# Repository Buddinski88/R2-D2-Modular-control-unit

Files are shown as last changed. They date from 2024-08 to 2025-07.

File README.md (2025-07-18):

# R2D2 Modular control unit (MCU)

## General motivation
- There are many good solutions for organizing all the control electronics for the whole selection of R2D2 bodys.
- However, none of these solutions fully met my requirements, so I designed my own interpretation of a modular control unit `the brain`.
  - Special thanks to everyone who inspired me, particularly John van Ohrs with his [R2D2 modular electronics panel by jfmvoers - Thingiverse](https://www.thingiverse.com/thing:6580609) and Tim Eebel with his [MarkIII Hinged Electronics Panel](https://www.printables.com/model/614178-markiii-hinged-electronics-panel).

## Requirements
- The module must be completely removable as a single unit to allow work on it at the workbench.
  - Everything must be possible without any special tools, i.e., plug-and-play instead of screws (almost achieved)!
- To allow access when installed, the entire unit must be hinged (no tools required for this step).
- The design must be modular, allowing it to be adapted to specific requirements.
- The design must be based on a grid (60x60mm) and offers panels ranging from `1x1` to `NxN`.

## Used Mods & Kudos

<blockquote class="callout note">
💡 <strong>NOTE:</strong> The following list contains an overview of the mods that I currently use in my Droid. It is not mandatory to use them as well, but I can confirm that they are compatible with each other.
</blockquote>

- [Battery Tray for Baddeley MKIII Astromech](https://www.printables.com/de/model/192002-battery-tray-for-baddeley-mkiii-astromech) by [Jason Charlton | Printables.com](https://www.printables.com/de/@JasonCharlton_264357) (he also has many other great mods!)
- Dome Motor Mount by [Gonz Pousada J Luis](https://www.facebook.com/groups/MrBaddeley/posts/3683034678691760/).
- Both Luis and Jason have other fantastic mods, and you should also check out [Jason's YouTube Channel](https://www.youtube.com/@jasonsR2D2).
- A special thanks to Ben from [Printed Droid](https://printed-droid.com), who provided me with the electronic components, and to Norbert A. Richartz, who is developing the AstroCan System and [BetterDuinoFirmwareV4](https://github.com/RealNobser/BetterDuinoFirmwareV4). He answered nearly all my questions and integrated some cool features.

## Images
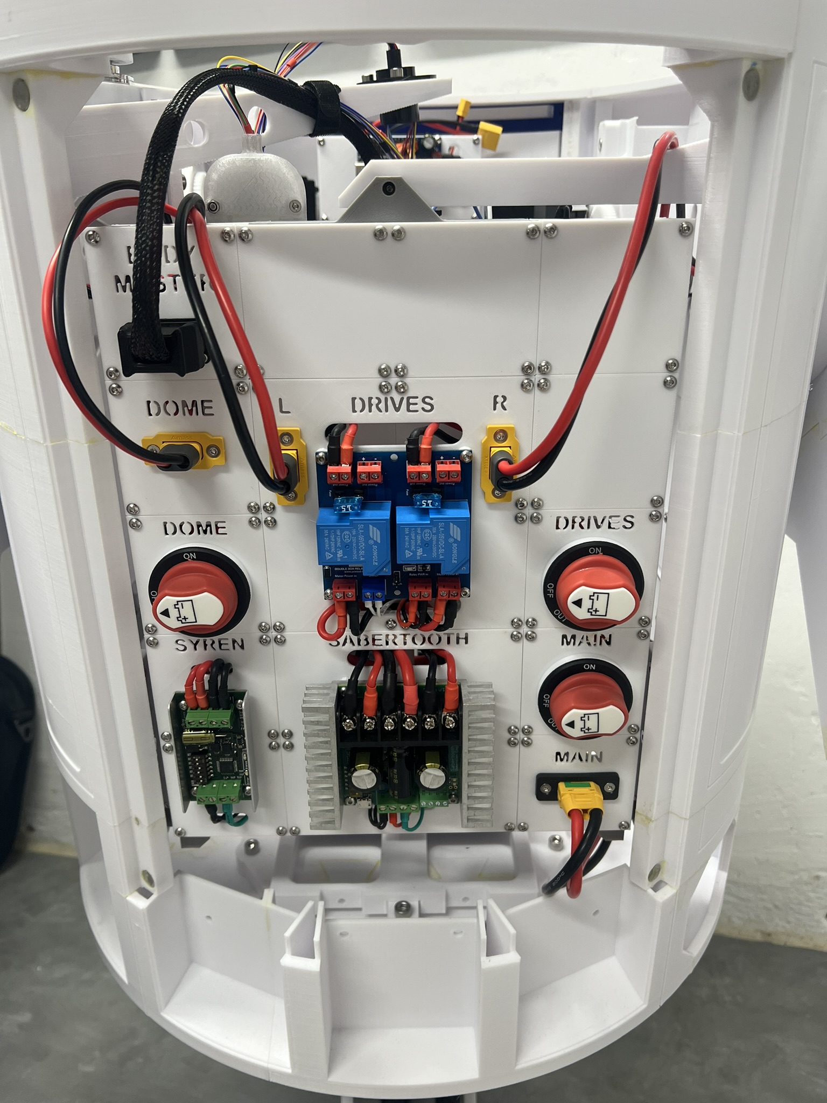
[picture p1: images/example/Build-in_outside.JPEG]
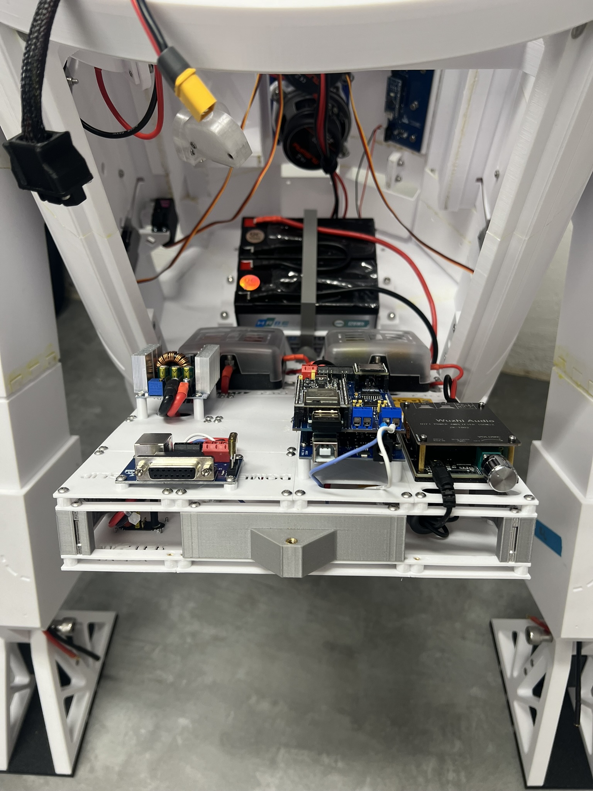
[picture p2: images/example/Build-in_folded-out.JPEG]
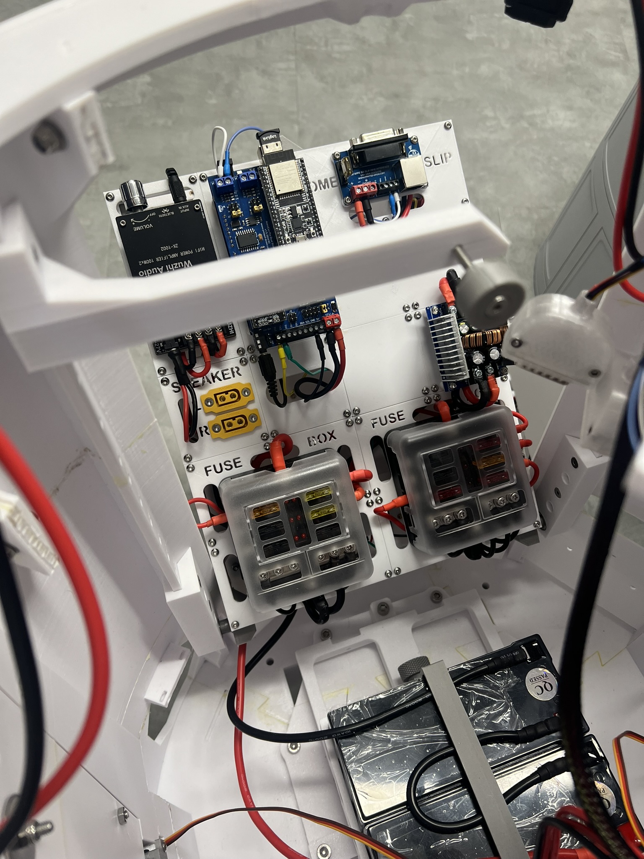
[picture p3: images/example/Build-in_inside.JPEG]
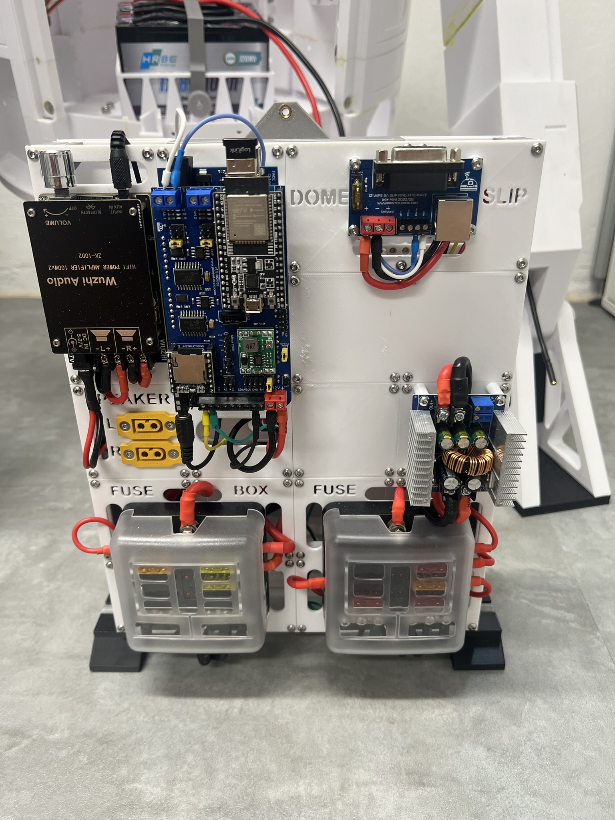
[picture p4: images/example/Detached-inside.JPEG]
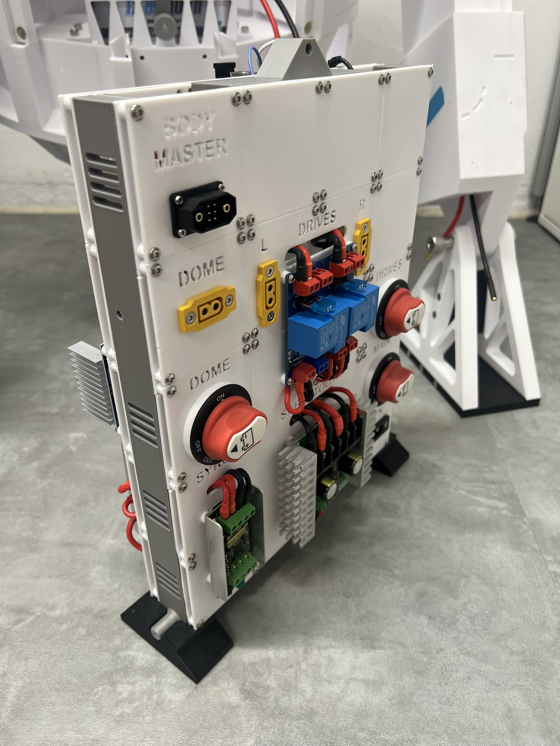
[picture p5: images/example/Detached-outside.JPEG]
    

## Community panels

<blockquote class="callout tip">
🛠 <strong>TIP:</strong> The following link contains an overview of panels which were created by other users to extend the option what electronics can be used. Thank you so much!
</blockquote>

[R2-D2 MCU-Panel-Collection](https://makerworld.com/de/collections/5528180-r2-d2-mcu-panel-collection)

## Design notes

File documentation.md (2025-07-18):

# Documentation Modular Control Unit (MCU)

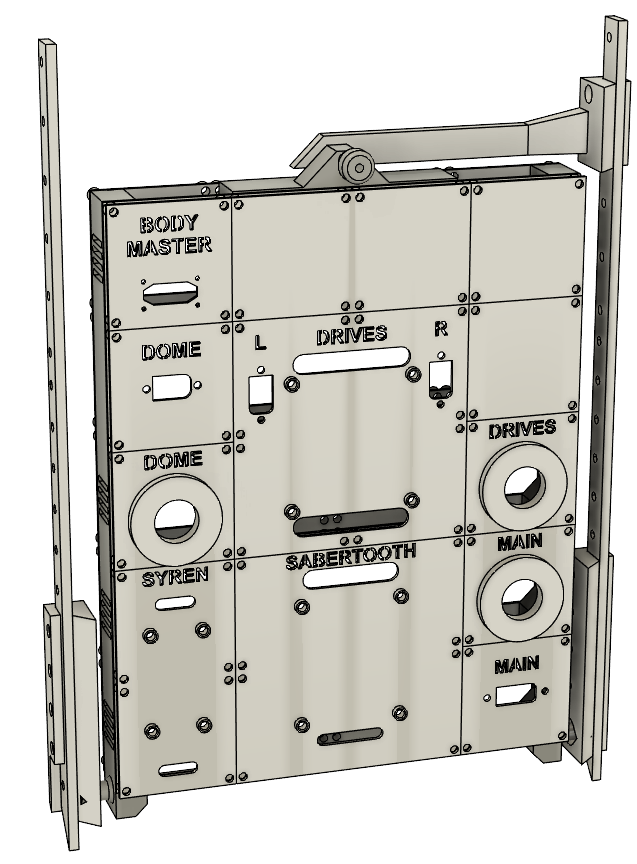
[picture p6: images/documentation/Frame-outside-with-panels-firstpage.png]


<p style="text-align: center;">Version 1.2 created by Bastian Oelkuch with Fusion360</p>

# Table of content
- [Documentation Modular Control Unit (MCU)](#documentation-modular-control-unit-mcu)
- [Table of content](#table-of-content)
  - [General description and requirements](#general-description-and-requirements)
  - [Overview of the design](#overview-of-the-design)
    - [Frame](#frame)
    - [Panels](#panels)
  - [Parts list](#parts-list)
    - [Screws and Nuts](#screws-and-nuts)
    - [Threaded inserts, Standoffs \& Bearings](#threaded-inserts-standoffs--bearings)
    - [Connectors and Switches](#connectors-and-switches)
    - [Boards](#boards)
  - [Assembly instructions for the Frame](#assembly-instructions-for-the-frame)
    - [1. Preparation of the Body Adapters](#1-preparation-of-the-body-adapters)
    - [2. Preparation of the Frame](#2-preparation-of-the-frame)
    - [3. Assembly the Frame](#3-assembly-the-frame)
    - [4. Assembly of the screwable Body Adapter](#4-assembly-of-the-screwable-body-adapter)
    - [5. Assembly and disassembly on the Body](#5-assembly-and-disassembly-on-the-body)
      - [5.1 Assembly](#51-assembly)
      - [5.2 Disassembly](#52-disassembly)
    - [6. Assembly instructions to attach the panels](#6-assembly-instructions-to-attach-the-panels)
  - [Community panels](#community-panels)

<blockquote class="callout warning">
⚠️ <strong>WARNING:</strong> I am not a trained electrician and cannot take any responsibility for any damage or injury that may occur.
</blockquote>

<blockquote class="callout tip">
   🛠 <strong>TIP:</strong> Have a look at the <a href="https://github.com/Buddinski88/R2-D2-Modular-body-backpack">R2-D2 Modular Body Backpack</a> if you also want a flexible solution to mount electronics to the Body of your R2 unit.
</blockquote>

## General description and requirements
- All files have numbers at the end `d1x1` means that the panel has a size of 60x60mm.
- The panels only have the size at the end because the quantity depends on your setup. Only in some cases you will find `x2` at the end. E.g. for the Stand.

## Overview of the design

### Frame

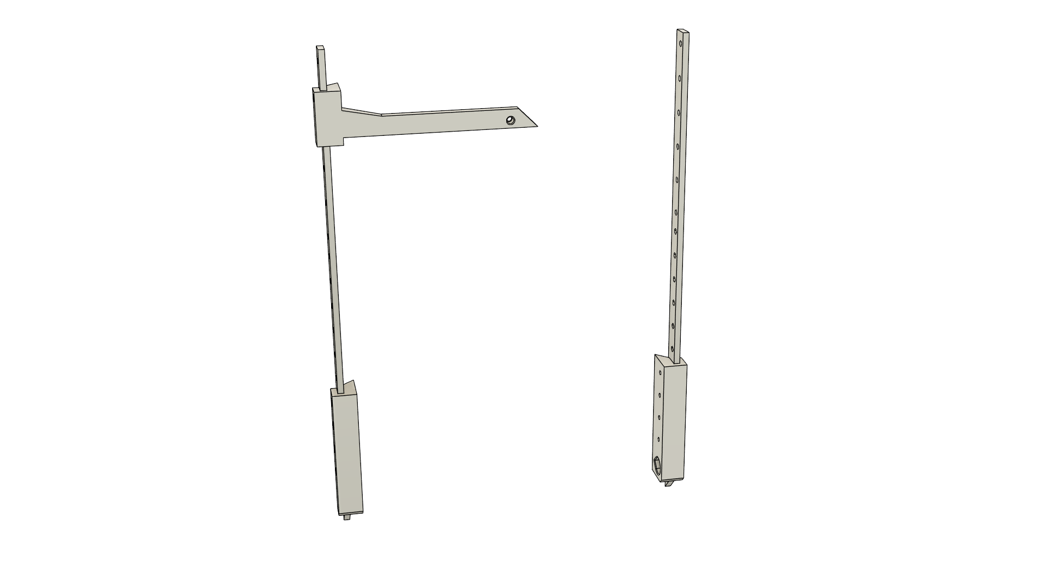
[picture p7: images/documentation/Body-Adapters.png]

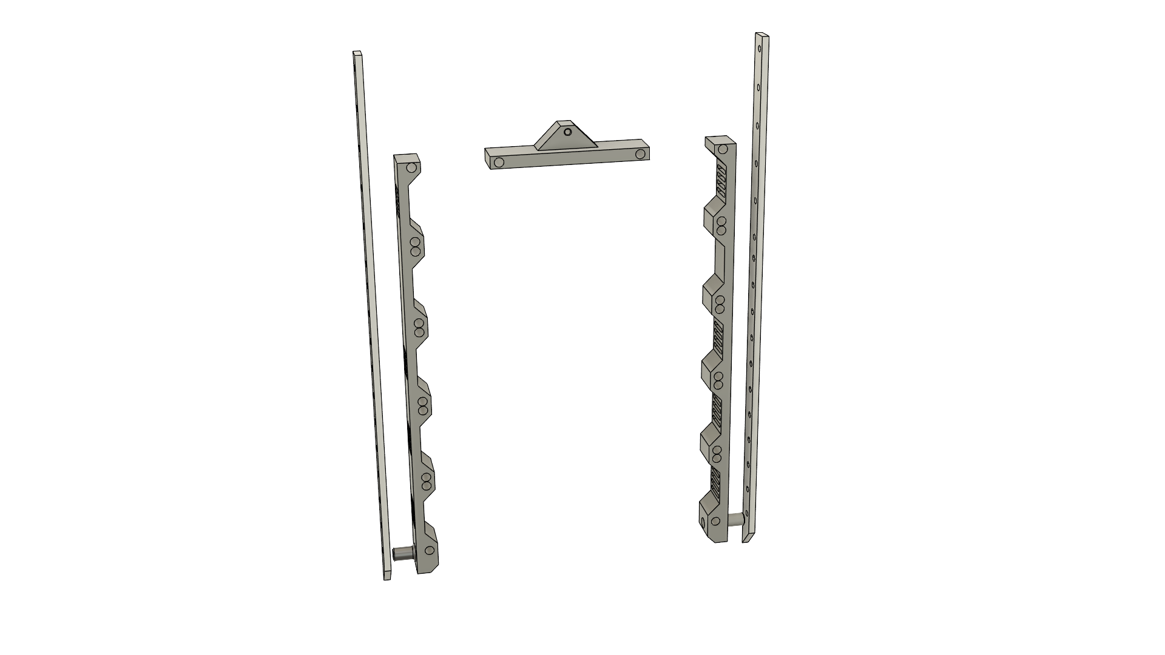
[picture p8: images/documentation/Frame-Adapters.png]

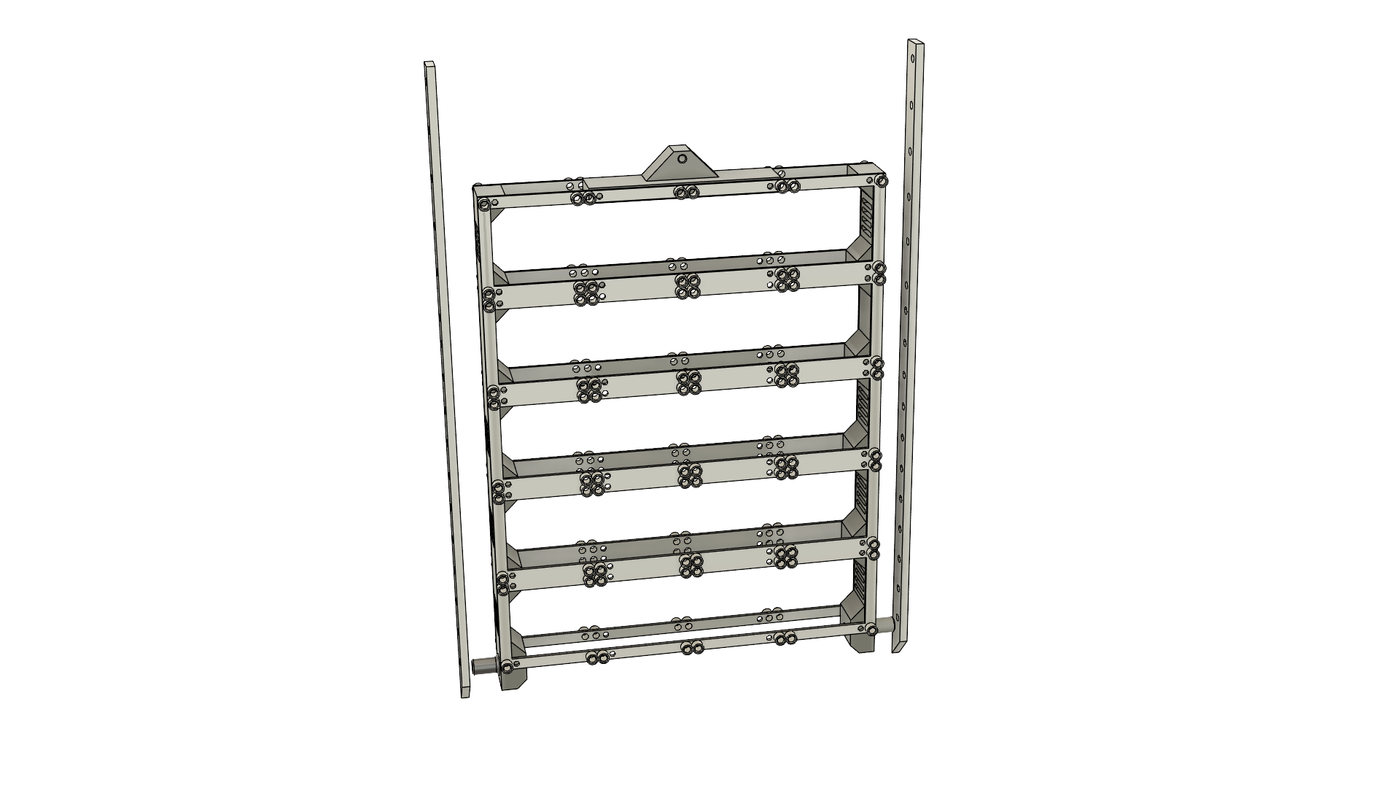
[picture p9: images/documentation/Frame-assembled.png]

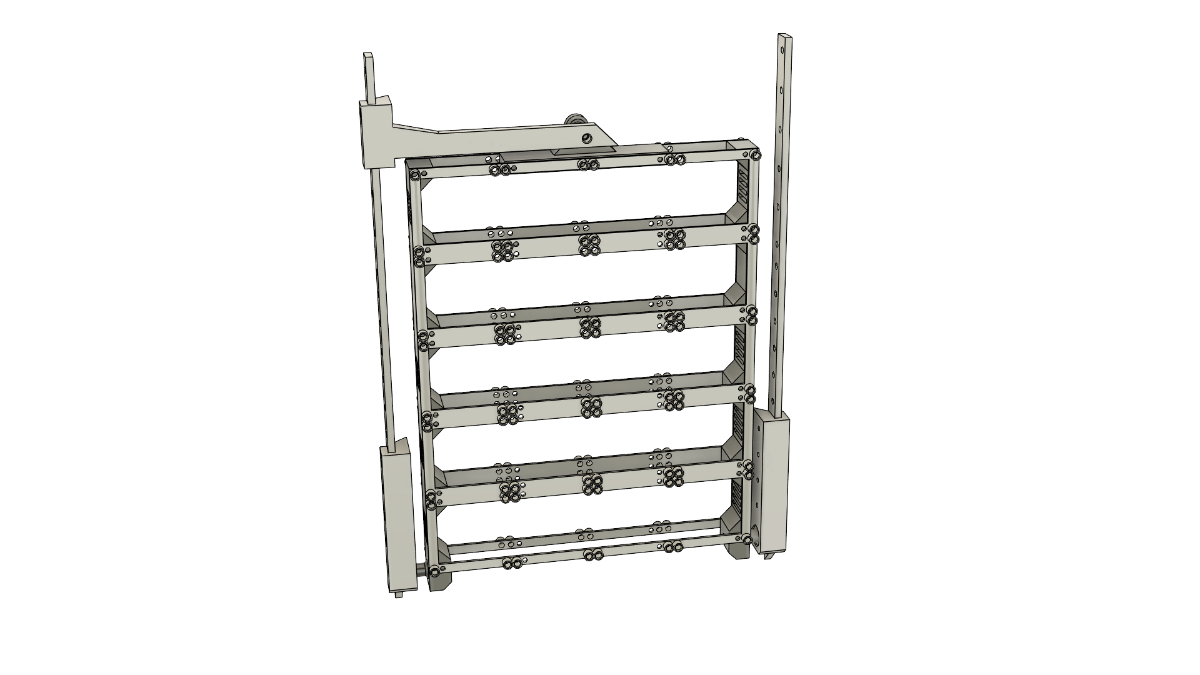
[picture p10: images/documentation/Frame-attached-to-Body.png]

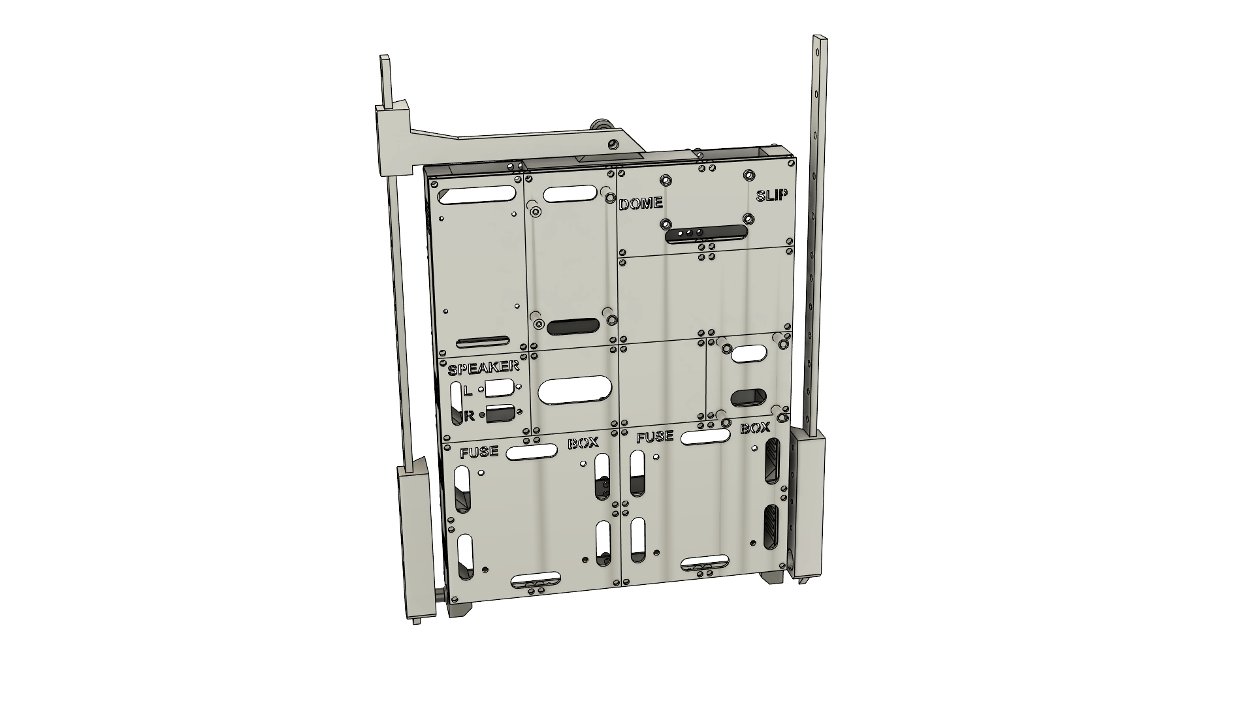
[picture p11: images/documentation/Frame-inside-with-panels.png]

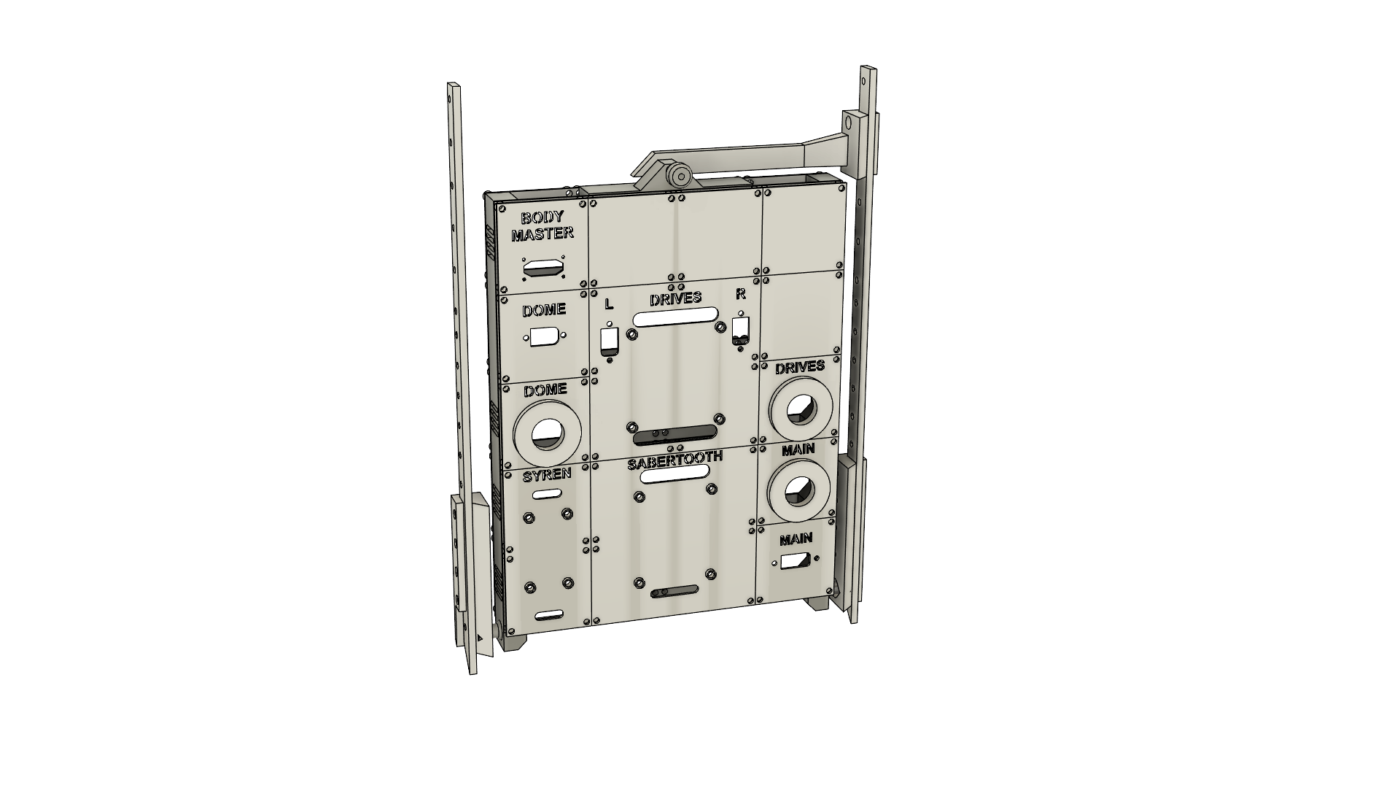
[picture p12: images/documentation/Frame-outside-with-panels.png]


### Panels

| Name | Screenshot |
| --- | --- |
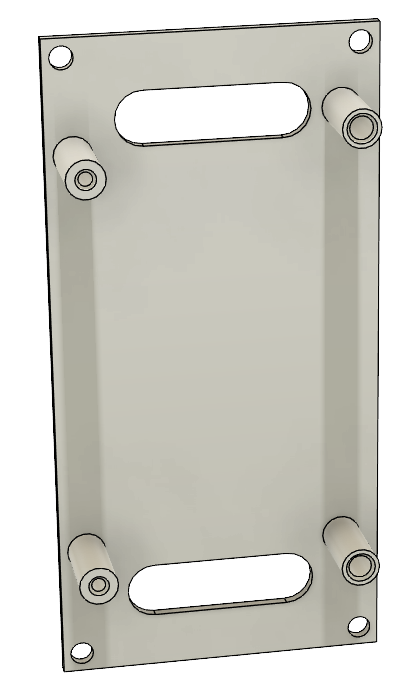
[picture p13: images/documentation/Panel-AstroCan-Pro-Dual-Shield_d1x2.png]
| Panel-AstroCan-Pro-Dual-Shield_d1x2.stl |  |
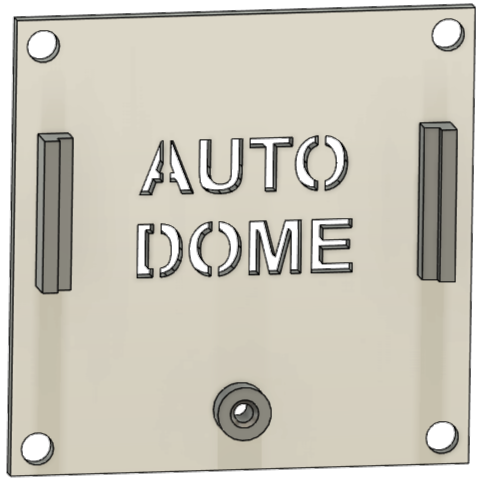
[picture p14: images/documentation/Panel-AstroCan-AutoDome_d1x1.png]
| Panel-AstroCan-AutoDome_d1x1.stl |  |
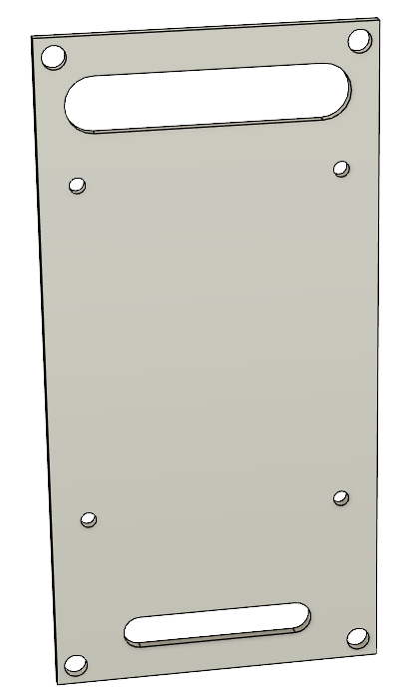
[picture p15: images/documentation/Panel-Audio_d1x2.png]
| Panel-Audio_d1x2.stl |  |
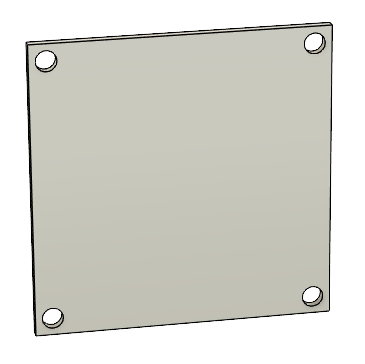
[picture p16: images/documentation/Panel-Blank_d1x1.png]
| Panel-Blank_d1x1.stl|  |
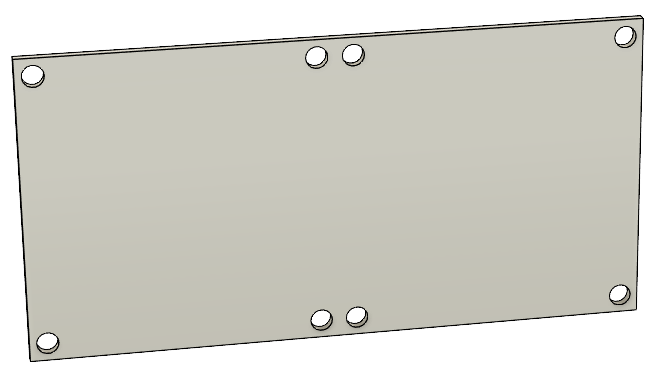
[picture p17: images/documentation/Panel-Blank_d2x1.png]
| Panel-Blank_d2x1.stl |  |
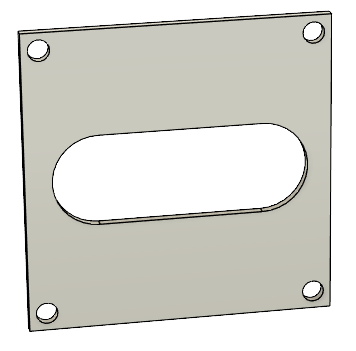
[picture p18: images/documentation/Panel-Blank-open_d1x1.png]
| Panel-Blank-open_d1x1.stl |  |
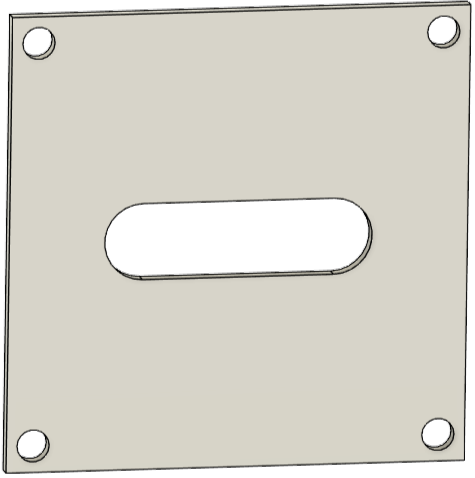
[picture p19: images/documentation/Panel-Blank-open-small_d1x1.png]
| Panel-Blank-open-small_d1x1.stl |  |
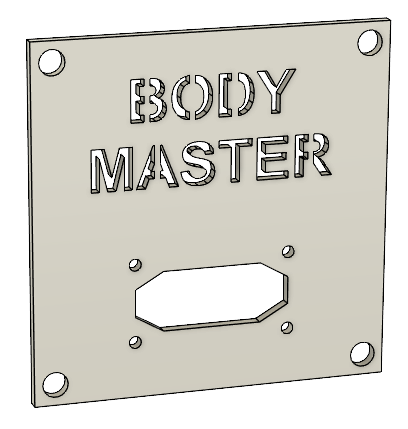
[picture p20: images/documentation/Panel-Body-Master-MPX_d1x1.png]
| Panel-Body-Master-MPX_d1x1.stl |  |
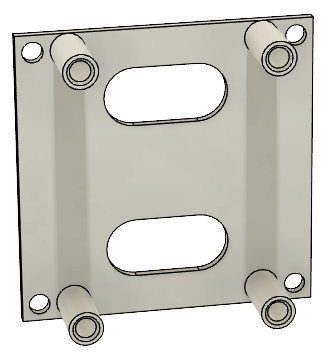
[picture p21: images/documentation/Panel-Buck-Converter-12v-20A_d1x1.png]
| Panel-Buck-Converter-12v-20A_d1x1.stl |  |
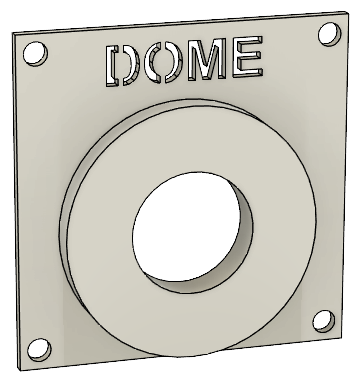
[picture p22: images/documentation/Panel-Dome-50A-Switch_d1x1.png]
| Panel-Dome-50A-Switch_d1x1.stl |  |
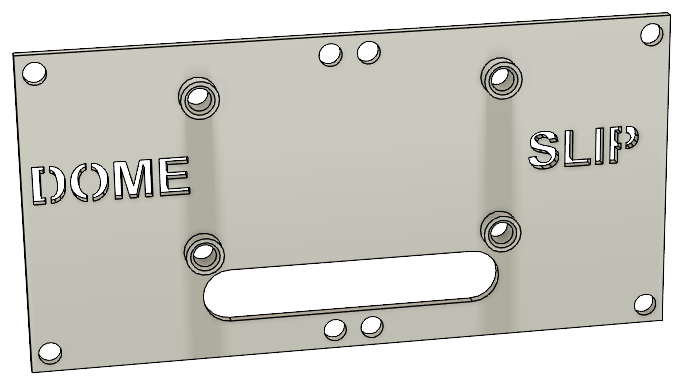
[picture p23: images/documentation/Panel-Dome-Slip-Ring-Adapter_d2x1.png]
| Panel-Dome-Slip-Ring-Adapter_d2x1.stl |  |
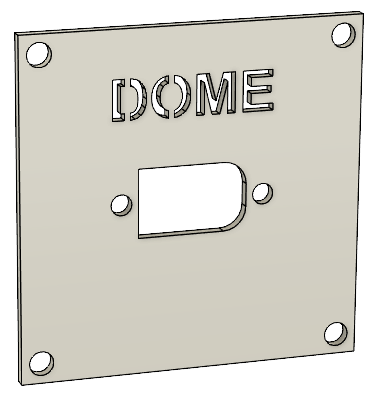
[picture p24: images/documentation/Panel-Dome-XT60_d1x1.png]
| Panel-Dome-XT60_d1x1.stl |  |
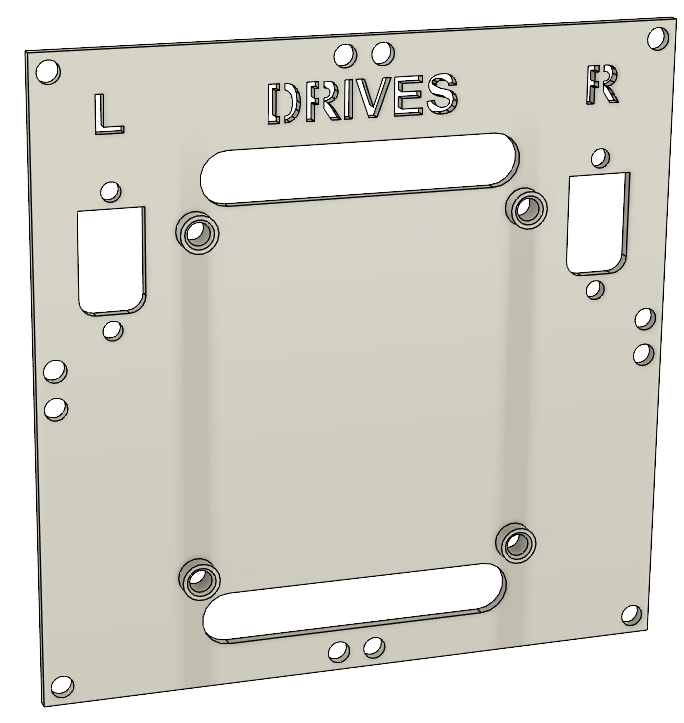
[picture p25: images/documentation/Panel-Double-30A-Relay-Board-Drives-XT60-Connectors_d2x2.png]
| Panel-Double-30A-Relay-Board-Drives-XT60-Connectors_d2x2.stl |  |
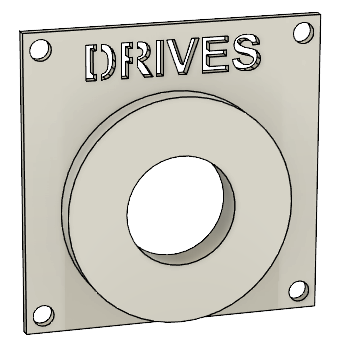
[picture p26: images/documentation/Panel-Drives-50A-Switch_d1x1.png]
| Panel-Drives-50A-Switch_d1x1.stl |  |
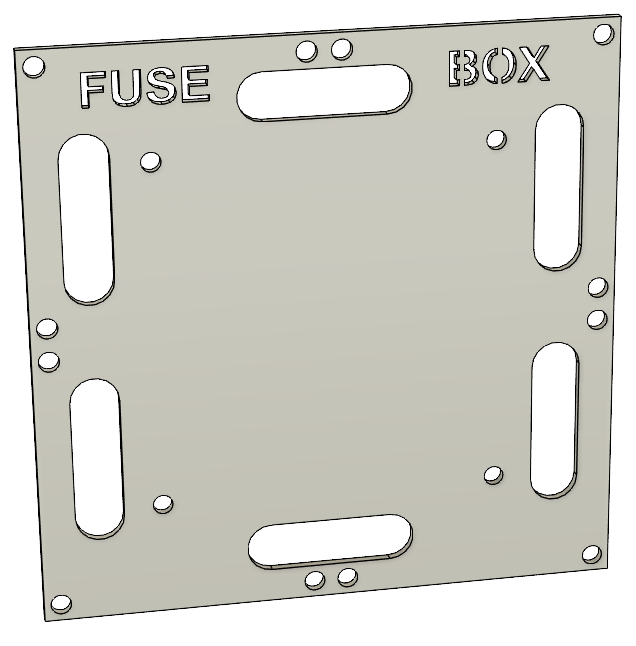
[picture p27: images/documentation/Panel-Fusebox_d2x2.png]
| Panel-Fusebox_d2x2.stl |  |
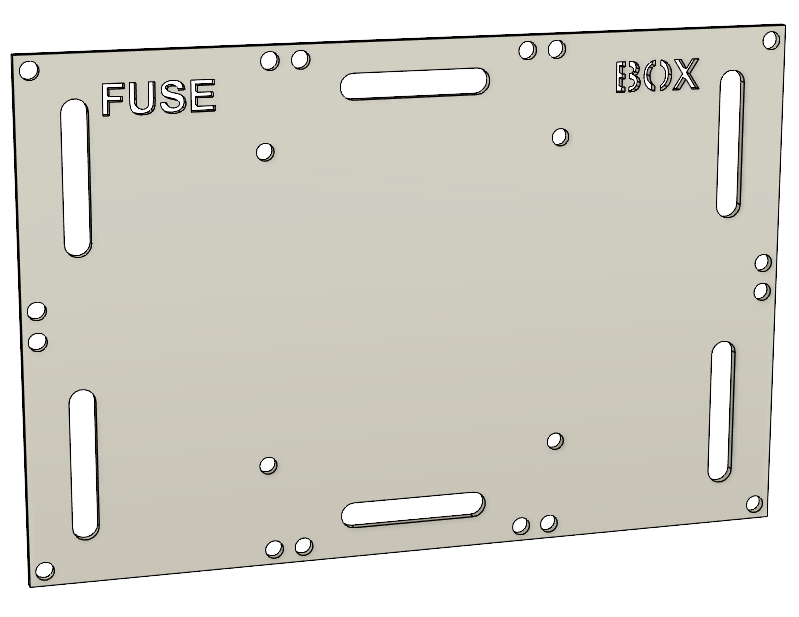
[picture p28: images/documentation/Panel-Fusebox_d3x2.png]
| Panel-Fusebox_d3x2.stl |  |
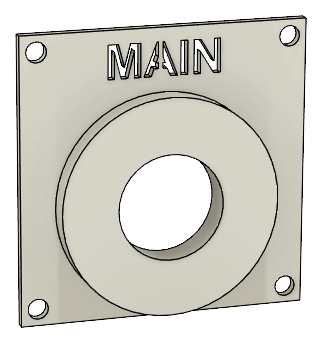
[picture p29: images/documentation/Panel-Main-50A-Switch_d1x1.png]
| Panel-Main-50A-Switch_d1x1.stl |  |
| Panel-Main-XT90_d1x1.stl |  |
| Panel-PDB-12V_d1x2.stl |  |
| Panel-PDB-24V_d1x2.stl |  |
| Panel-PDB-Modular_d2x1.stl |  |
| Panel-Sabertooth-32A_d2x2.stl |  |
| Panel-Speaker-XT60_d1x1.stl |  |
| Panel-Speaker-XT60-V2_d1x1.stl |  |
| Panel-Switch-Left-Leg_d1x1.stl |  |
| Panel-Switch-Right-Leg_d1x1.stl |  |
| Panel-Syren-10A_d2x1.stl |  |
| Panel-XT60-Left-Leg_d1x1.stl |  |
| Panel-XT60-Right-Leg_d1x1.stl |  |
| Stand_x2.stl | 

## Parts list

### Screws and Nuts

| Type | Quantity | Used for | Link |
| --- | --- | --- | ---- |
| **M2x10 mm Cylinder Head Screw** | **8** | Attaching amplifier and MPX-like connector to printed panels | |
| **M2x10 mm Cylinder Head Screw** | **2** | Attaching Arduino Mega2560 + AstroCan Shield to the printed panel | |
| **M2x10 mm Cylinder Head Screw** | **1** | Attaching AstroCan AutoDome to the printed panel | |
| **M3x6 mm Pan Head Screw** | **102**  | 80 for connecting the front and back frame to the standoffs | |
| | | 2 for attaching Arduino Mega2560 + AstroCan Shield to the printed panel | |
| | | 4 for attaching Sabertooth to the printed panel | |
| | | 4 for attaching Syren  to the printed panel | |
| | | 4 for attaching Relay board  to the printed panel | |
| | | 4 for attaching Slipring-Adapter-PCB to the printed panel | |
| | | 4 for attaching 12V 20A buck converter to the printed panel | |
| **M3x10 mm Countersunk Screw** | **12** | Attaching the XT60 & XT90 to the adapters | |
| **M3x12 mm Countersunk Screw** | **8** | Attaching the fuse boxes to printed panels | |
| **M3 Locknut** | **20** | 8 for attaching fuse boxes to printed panels | |
| | | 12 for attaching XT60 & XT90 to the adapters | |
| **M4x18 mm Countersunk Screw** | **4** | Connecting the `Body-Adapter-left.stl` and `Body-Adapter-right.stl` to the body | |
| **M4x25 mm Countersunk Screw** | **2** | Screwing the `Frame-Adapter-pin-left.stl` and `Frame-Adapter-pin-right.stl` to `Frame-Connector-left.stl` and `Frame-Connector-right.stl` | |
| **M4x40 mm Countersunk Screw** | **1** | Securing the MCU in the body using `Body-Adapter-Top-Knob.stl` | |
| **M4 Square Nut** | **1** | Securing the MCU in the body using `Body-Adapter-Top-Knob.stl` | |

### Threaded inserts, Standoffs & Bearings

| Type | Quantity | Used for | Link |
| --- | --- | --- | ---- |
| **M2x3x3.2 mm Threaded Insert**  | **3** | To attach the AstroCan DualShield to the `Panel-AstroCan-Pro-Dual-Shield_d1x2.stl` panel and AstroCan AutoDome to the `Panel-AstroCan-AutoDome_d1x1.stl` |
| **M3x5.7 mm Threaded Insert** | **160**  | To fill all available inserts on the frame (additional inserts may be required based on panel used) | [Amazon](https://www.amazon.de/gp/product/B08BCRZZS3) |
| **M4x4x6 mm Threaded Insert** | **4** | Connecting `Body-Adapter-left.stl` and `Body-Adapter-right.stl` to the body | |
| **M3x25 mm Standoffs** | **40** | Connecting the `Frame-Complete_x2.stl` (if you have a big enougth printer) or `Frame-Modular-End_x4.stl` and `Frame-Modular-Middle_x6.stl` to the frame adapters | [AliExpress](https://de.aliexpress.com/item/1005003175580805.html) |
| **15x10x4 mm Bearings** | **4** | Two each for `Body-Adapter-left.stl` and `Body-Adapter-right.stl` | |

### Connectors and Switches

| Type | Quantity | Used for | Link |
| --- | --- | --- | ---- |
| **XT60 Connector** | **5** | Connection to left and right drive, dome, and speakers | [AliExpress](https://de.aliexpress.com/item/1005006156272920.html) |
| **XT90 Connector** | **1** | Main power connection of the batteries | [AliExpress](https://de.aliexpress.com/item/1005004462521219.html) |
| **MPX-like Connector** | **2** | To provide a power connection with power and up to 6 data lines to the body | [AliExpress](https://de.aliexpress.com/item/1005001997107973.html) |
| **50V 50A Power Switch** | **3** | To switch the dome, drives, and main power | [AliExpress](https://de.aliexpress.com/item/1005004328677834.html) |
| 7P Powerrails | **0** | Optional for 12/24V power distribution | [AliExpress](https://de.aliexpress.com/item/4001073019784.html)

### Boards

| Type | Quantity | Used for | Link |
| --- | --- | --- | ---- |
| **5,5-30V 3A LCD Step-down** | **1** | Power supply for 12V to AstroCan Shield | [AliExpress](https://de.aliexpress.com/item/1005002777283109.html) |
| **5,5-30V 3A LCD Step-down** | **1** | Power supply for 5V to AstroCan AutoDome | [AliExpress](https://de.aliexpress.com/item/1005002777283109.html) |
| **5V 15A Buck Converter** | **2** | Power supply for 5V | [AliExpress](https://de.aliexpress.com/item/1005006506300187.html) |
| **12V 20A Buck Converter** | **1** | Power supply for 12V | [Amazon](https://www.amazon.de/dp/B09GLT7RVS) |
| **SyRen 10A** | **1** | Controller for Dome motor | [RobotShop.com](https://eu.robotshop.com/de/products/syren-10a-6v-24v-regenerativer-motortreiber) |
| **Sabertooth Dual 2x32A** | **1** | Controller for Drive motors | [RobotShop.com](https://eu.robotshop.com/de/products/sabertooth-dual-2x32a-6v-24v-regenerativer-motortreiber) |
| **Double 30 Relay Board** | **1** | Cut the power to between motors and Sabertooth | [printed-droid.com](https://shop.printed-droid.com/produkt/30a-relay-board/) |
| **12 Wire 8A Slip Ring Interface**  | **1** | Connect Dome to Body | [printed-droid.com](https://shop.printed-droid.com/produkt/fused-12-wire-slipring-interface-2022/) |
| **AstroCan Pro Dual Shield** | **1** | "The Brain" | [printed-droid.com](https://shop.printed-droid.com/produkt/astrocan-pro-dual-shield/) |
| **AstroCan AutoDome** | **1** | Control the Dome Motor | [printed-droid.com](https://shop.printed-droid.com/produkt/astrocan-autodome/) |
| **Hifi Amplifier** | **1** | Audiointerface | [Amazon](https://www.amazon.de/ZHITING-Bluetooth-Verst%C3%A4rkerplatine-Audioverst%C3%A4rkerplatine-LC-Filtertechnik-Zweikanal-DC8-24V/dp/B088N6Z9TB) |
| Alternative **Hifi Amplifier** without Bluetooth | **1** | Audiointerface | [Amazon](https://www.amazon.de/dp/B09PL6R1L7) |
| **Fusebox** | **2** | To get everything secured | [AliExpress](https://de.aliexpress.com/item/1005005923377932.html) |

## Assembly instructions for the Frame

<blockquote class="callout note">
💡 <strong>NOTE:</strong> The assembly is relatively simple, as the entire "package/unit" is stable once it has been assembled.
</blockquote>

**Required Parts**:
- **15x10x4 mm bearings (4 pieces)**
- **M4x4x6 mm threaded inserts (8 pieces)**
- **M3x18 mm countersunk screws (5 pieces)**
- **M3x6 mm pan head screws (80 pieces)**
- **M4 square nut (1 piece)**
- **M4x40 mm countersunk screw (1 piece)**
- **M3x25 mmStandoffs (40 pieces)**

### 1. Preparation of the Body Adapters
1. **Body-Adapter-left.stl** and **Body-Adapter-right.stl**:
   1. Press in **two 15x10x4 mm bearings** each.
   2. Melt in **two M4x4x6 mm threaded inserts** each.
   3. Attach to the body using **two M3x18 mm countersunk screws** each, ensuring that the bottom edge of the adapters aligns with the mounting points on the body.
   4. **Optional**: If necessary, two additional screws and threaded inserts can be installed on each side.

### 2. Preparation of the Frame

<blockquote class="callout note">
💡 <strong>NOTE:</strong> If the build volume is larger than that of a Bambu Lab X1C, <code>Frame-Complete_x2.stl</code> can be printed twice. If the build volume is smaller than that of a Bambu Lab X1C, `Frame-Modular-End_x4.stl` must be printed four times and `Frame-Modular-Middle_x6.stl` six times.
</blockquote>

1. Melt in **80 M3x5.7 mm threaded inserts** per side (fewer inserts may be used depending on how the modules are arranged).

### 3. Assembly the Frame
1. Attach the **40 M3x25 mm standoffs** to one side of the frame using **40 M3x6 mm pan head screws**.
2. Screw the `Frame-Connector-pin-left.stl` and `Frame-Connector-pin-right.stl` to the corresponding Frame-Connectors with a **M4x25 mm Countersunk Screw**.
3. Slide the parts `Frame-Connector-left.stl`, `Frame-Connector-right.stl`, and `Frame-Connector-top.stl` over the standoffs.
4. Finally, attach the remaining side to the standoffs using **40 M3x6 mm pan head screws**.

### 4. Assembly of the screwable Body Adapter
1. `Body-Frame-Adapter-top.stl` and `Body-Frame-Adapter-top-Knob.stl`:
   1. Melt in **one M4x4x6 mm threaded insert**.
   2. Attach to the body using **one M4x18 mm countersunk screw**, ensuring that the top edge of the adapter aligns with the mounting point on the body.
   3. Assemble the hand-tightened knob using **one M4 square nut** and **one M4x40 mm countersunk screw**.

### 5. Assembly and disassembly on the Body
**Required Parts**:
- **M4x18 mm countersunk screws (4 pieces)**
- **M4x40 mm countersunk screw (1 piece)**
- **M4 square nut (1 piece)**
- **M4x4x6 mm threaded inserts (4 pieces)**
- **15x10x4 mm bearings (4 pieces)**

#### 5.1 Assembly
1. **Attach** `Body-Adapter-left.stl`:
   - Screw the left adapter with the 15x10x4 mm bearings and attach it to the body.

2. **Insert the MCU**:
   - Insert the MCU into the left adapter (`Body-Adapter-left.stl`).

3. **Mount** `Body-Adapter-right.stl`:
   - Place the `Body-Adapter-right.stl` onto the MCU.

4. **Secure Adapter to the Body**:
   - Slide the right adapter onto the body, tilt slightly, and then tighten the screws.

#### 5.2 Disassembly
- Follow the steps in reverse order.

### 6. Assembly instructions to attach the panels

- The panels themselves are each attached to the frame with **1-n M3x6 mm pan head screws**.
- In some cases, **M3x5.7 mm threaded inserts** are also required to attach the parts to the panels themselves.

## Community panels

<blockquote class="callout tip">
🛠 <strong>TIP:</strong> The following link contains an overview of panels which were created by other users to extend the option what electronics can be used. Thank you so much!
</blockquote>

[R2-D2 MCU-Panel-Collection](https://makerworld.com/de/collections/5528180-r2-d2-mcu-panel-collection)

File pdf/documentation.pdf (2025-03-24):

# Documentation Modular Control Unit (MCU)


Version 1.1 created by Bastian Oelkuch with Fusion360

# Table of content

Documentation Modular Control Unit (MCU) Table of content
General description and requirements Overview of the design
Frame
Panels
Parts list
Screws and Nuts
Threaded inserts, Standoffs & Bearings Connectors and Switches
Boards
Assembly Instructions for the Frame
1. Preparation of the Body Adapters
2. Preparation of the Frame
3. Assembly the Frame
4. Assembly of the Screwable Body Adapter Assembly on the Body
Assembly Instructions:
Disassembly:
Assembly instructions panels Community panels

[!WARNING]
I am not a trained electrician and cannot take any responsibility for any damage or injury that may occur.

## General description and requirements

All files have numbers at the end d1x1 means that the panel has a size of 60x60mm. The panels only have the size at the end because the quantity depends on your setup. Only in some cases you will find x2 at the end. E.g. for the Stand.

## Overview of the design

### Frame


### Panels

Name | Screenshot


Panel-AstroCan-Pro-Dual-Shield_d1x2.stl


Panel-Audio_d1x2.stl

Panel-Blank_d1x1.stl

Panel-Blank_d2x1.stl

Panel-Blank-open_d1x1.stl


Panel-Body-Master-MPX_d1x1.stl

Name | Screenshot


Panel-Buck-Converter-12v-20A_d1x1.stl


Panel-Dome-50A-Switch_d1x1.stl

Panel-Dome-Slip-Ring-Adapter_d2x1.stl


Panel-Dome-XT60_d1x1.stl


Panel-Double-30A-Relay-Board-Drives-XT60-
Connectors_d2x2.stl

Panel-Drives-50A-Switch_d1x1.stl

Panel-Fusebox_d2x2.stl

Name | Screenshot

Panel-Fusebox_d3x2.stl


Panel-Main-50A-Switch_d1x1.stl

Panel-Main-XT90_d1x1.stl


Panel-PDB-12V_d1x2.stl


Panel-PDB-24V_d1x2.stl

Panel-PDB-Modular_d2x1.stl

Name | Screenshot


Panel-Sabertooth-32A_d2x2.stl

Panel-Speaker-XT60_d1x1.stl

Panel-Switch-Left-Leg_d1x1.stl

Panel-Switch-Right-Leg_d1x1.stl


Panel-Syren-10A_d2x1.stl

Panel-XT60-Left-Leg_d1x1.stl

Name | Screenshot

Panel-XT60-Right-Leg_d1x1.stl

Stand_x2.stl

## Parts list

### Screws and Nuts

Type | Quantity Used for | Link

M2x10 mm
Cylinder
Head Screw

8

Attaching amplifier and MPX-like connector to printed panels

M2x10 mm
Cylinder
Head Screw

2

Attaching Arduino Mega2560 + AstroCan Shield to the printed panel

M3x6 mm
Pan Head
Screw

104

80 for connecting the front and back frame to the standoffs

2 for attaching Arduino Mega2560 + AstroCan Shield to the printed üanel

4 for attaching Sabertooth to the printed panel

4 for attaching Syren to the printed panel

4 for attaching Relay board to the printed panel

4 for attaching Slipring-Adapter-PCB to the printed panel

4 for attaching 12V 20A buck converter to the printed panel

M3x10 mm
Countersunk
Screw

### 12 Attaching the XT60 & XT90 to the adapters

M3x12 mm
Countersunk
Screw

### 8 Attaching the fuse boxes to printed panels

M3 Locknut | 20 | 8 for attaching fuse boxes to printed panels

12 for attaching XT60 & XT90 to the adapters

M4x18 mm
Countersunk
Screw

4

Connecting the Body-Adapter-left.stl and Body-Adapter-right.stl to the body

Type | Quantity Used for | Link

M4x25 mm

Countersunk Screw | 2 Screwing the Frame-Adapter-pin-left.stl and Frame-Adapter-pin-right.stl to Frame- Connector-left.stl and Frame-Connector- right.stl

M4x40 mm
Countersunk Screw | 1 Securing the MCU in the body using Body-Adapter- Top-Knob.stl
M4 Square Nut | 1 Securing the MCU in the body using Body-Adapter- Top-Knob.stl

### Threaded inserts, Standoffs & Bearings

Type | Quantity Used for | Link

M2x3x3.2
mm Threaded Insert | 2 To attach the AstroCan DualShield to the Panel- AstroCan-Pro-Dual-Shield_d1x2.stl panel

M3x5.7
mm Threaded Insert | 160 To fill all available recordings on the frame (additional inserts may be required based on panel used) | Amazon (https://www.amazon.de/gp/product/B08BCRZZS3)

M4x4x6
mm
Threaded
Insert

4

Connecting Body-Adapter-left.stl and Body-Adapter-right.stl to the body

M3x25
mm
Standoffs

40

Connecting the Frame-Complete_x2.stl (if you have a big enougth printer) or Frame-Modular-End_x4.stl and Frame-Modular-Middle_x6.stl to the frame adapters

AliExpress (https://de.aliexpress.com/item/1005003175580805.html)

15x10x4
mm
Bearings

4

Two each for Body-Adapter-left.stl and Body-Adapter-right.stl

### Connectors and Switches

Type | Quantity Used for | Link

XT60
Connector

5

Connection to left and right drive, dome, and speakers

AliExpress (https://de.aliexpress.com/item/1005006156272920.html)

XT90
Connector
| 1 | Main power connection of the batteries | AliExpress (https://de.aliexpress.com/item/1005004462521219.html)
MPX-like Connector | 2

To provide a power connection with power and
| | up to 6 data lines to the body | AliExpress (https://de.aliexpress.com/item/1005001997107973.html)
50V 50A Power Switch | 3 | To switch the dome, drives, and main power | AliExpress (https://de.aliexpress.com/item/1005004328677834.html)
7P Powerrails | 0 | Optional for 12/24V power distribution | AliExpress (https://de.aliexpress.com/item/4001073019784.html)

### Boards

Type | Quantity Used for | Link

5,5-30V 3A LCD Step-
down | 0 | Power supply for 5V | AliExpress (https://de.aliexpress.com/item/1005002777283109.html)
5V 15A Buck Converter | 2 | Power supply for 5V | AliExpress (https://de.aliexpress.com/item/1005006506300187.html)
12V 20A Buck Converter | 1 | Power supply for 12V | Amazon (https://www.amazon.de/dp/B09GLT7RVS)
SyRen 10A | 1 | Controller for Dome motor | RobotShop.com (https://eu.robotshop.com/de/products/syren-10a-6v-24v-regenerativer-motortreiber)
Sabertooth Dual 2x32A | 1 | Controller for Drive motors | RobotShop.com (https://eu.robotshop.com/de/products/sabertooth-dual-2x32a-6v-24v-regenerativer-motortreiber)
Double 30 Relay Board | 1 | Cut the power to between motors and Sabertooth | printed- droid.com (https://shop.printed-droid.com/produkt/30a-relay-board/)

### 12 Wire 8A Slip Ring

Interface

### 1 Connect Dome to Body

| | | printed- droid.com (https://shop.printed-droid.com/produkt/fused-12-wire-slipring-interface-2022/)

AstroCan Pro Dual
Shield

1 "The Brain"

| | | printed- droid.com (https://shop.printed-droid.com/produkt/astrocan-pro-dual-shield/)
Hifi Amplifier | 1 | Audiointerface | Amazon (https://www.amazon.de/ZHITING-Bluetooth-Verst%C3%A4rkerplatine-Audioverst%C3%A4rkerplatine-LC-Filtertechnik-Zweikanal-DC8-24V/dp/B088N6Z9TB)
Fusebox | 2 | To get everything secured | AliExpress (https://de.aliexpress.com/item/1005005923377932.html)

## Assembly Instructions for the Frame

[!NOTE]; been assembled.; Required Parts:; 15x10x4 mm bearings (4 pieces)

The assembly is relatively simple, as the entire "package/unit" is stable once it has

M4x4x6 mm threaded inserts (8 pieces) M3x18 mm countersunk screws (5 pieces) M3x6 mm pan head screws (80 pieces) M4 square nut (1 piece)
M4x40 mm countersunk screw (1 piece) M3x25 mmStandoffs (40 pieces)

### 1. Preparation of the Body Adapters

1. Body-Adapter-left.stl and Body-Adapter-right.stl:
1. Press in two 15x10x4 mm bearings each.
2. Melt in two M4x4x6 mm threaded inserts each.
3. Attach to the body using two M3x18 mm countersunk screws each, ensuring that the bottom edge of the adapters aligns with the mounting points on the body.
4. Optional: If necessary, two additional screws and threaded inserts can be installed on each side.

### 2. Preparation of the Frame

[!NOTE]

If the build volume is larger than that of a Bambu Lab X1C, Frame-Complete_x2.stl can be printed twice.
If the build volume is smaller than that of a Bambu Lab X1C, Frame-Modular-End_x4.stl must be printed four times and Frame-Modular-Middle_x6.stl six times.
1. Melt in 80 M3x5.7 mm threaded inserts per side (fewer inserts may be used depending on how the modules are arranged).

### 3. Assembly the Frame

1. Attach the 40 M3x25 mm standoffs to one side of the frame using 40 M3x6 mm pan head screws.
2. Screw the Frame-Connector-pin-left.stl and Frame-Connector-pin-right.stl to the corresponding Frame-Connectors with a M4x25 mm Countersunk Screw.
3. Slide the parts Frame-Connector-left.stl, Frame-Connector-right.stl, and Frame-Connector-top.stl over the standoffs.
4. Finally, attach the remaining side to the standoffs using 40 M3x6 mm pan head screws.

### 4. Assembly of the Screwable Body Adapter

1. Body-Frame-Adapter-top.stl and Body-Frame-Adapter-top-Knob.stl:
1. Melt in one M4x4x6 mm threaded insert.
2. Attach to the body using one M4x18 mm countersunk screw, ensuring that the top edge of the adapter aligns with the mounting point on the body.
3. Assemble the hand-tightened knob using one M4 square nut and one M4x40 mm countersunk screw.

### Assembly on the Body

Required Parts:

M4x18 mm countersunk screws (4 pieces) M4x40 mm countersunk screw (1 piece) M4 square nut (1 piece)
M4x4x6 mm threaded inserts (4 pieces) 15x10x4 mm bearings (4 pieces)

Assembly Instructions:

1. Attach Body-Adapter-left.stl: Screw the left adapter with the 15x10x4 mm bearings and attach it to the body.
2. Insert the MCU:
Insert the MCU into the left adapter (Body-Adapter-left.stl).
3. Mount Body-Adapter-right.stl:

Place the Body-Adapter-right.stl onto the MCU.
4. Secure Adapter to the Body: Slide the right adapter onto the body, tilt slightly, and then tighten the screws.

Disassembly:

Follow the steps in reverse order.

### Assembly instructions panels

The panels themselves are each attached to the frame with 1-n M3x6 mm pan head screws.
In some cases, M3x5.7 mm threaded inserts are also required to attach the parts to the panels themselves.

## Community panels

[!NOTE]

The following list contains an overview of panels which were created by other users
to extend the option what electronics can be used. Thank you so much!
Stephen Mathis has published his created panels (https://www.facebook.com/groups/2152999025028674/?multi_permalinks=3957991467862745) on the Facebook group of Mr. Baddeley. He also posted a video. (https://www.facebook.com/share/v/1Ft1YTVtmM/)
dadmin (https://makerworld.com/de/@user_2838957196) created a set of panels (https://makerworld.com/de/models/1222082-r2d2-custom-panels-for-r2d2-modular-control-unit) to hold electronics like a voltmeter, new power terminals, Sparkfun MP3 Trigger, new AMP, XBOX receiver and Mini Maestro 24-Channel USB controller.

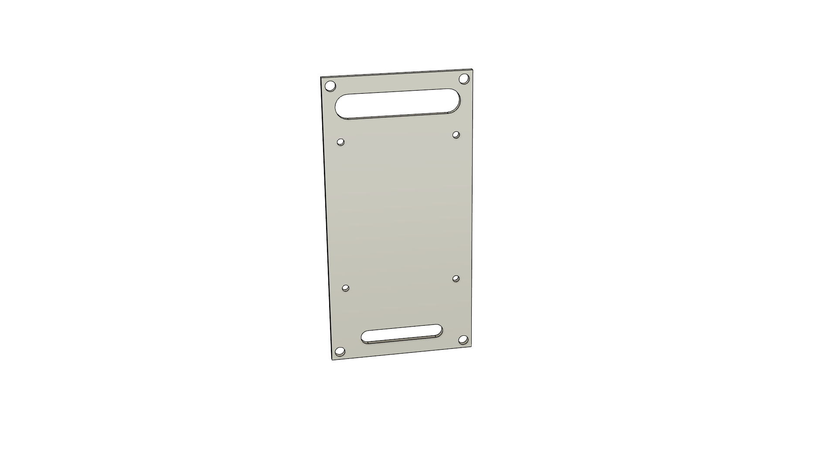
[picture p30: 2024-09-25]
images/documentation/fullsize/Panel-Audio_d1x2.png

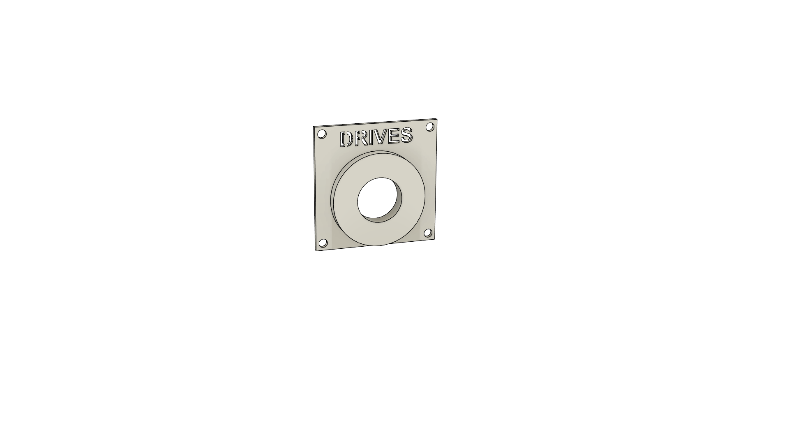
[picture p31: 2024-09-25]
images/documentation/fullsize/Panel-Drives-50A-Switch_d1x1.png

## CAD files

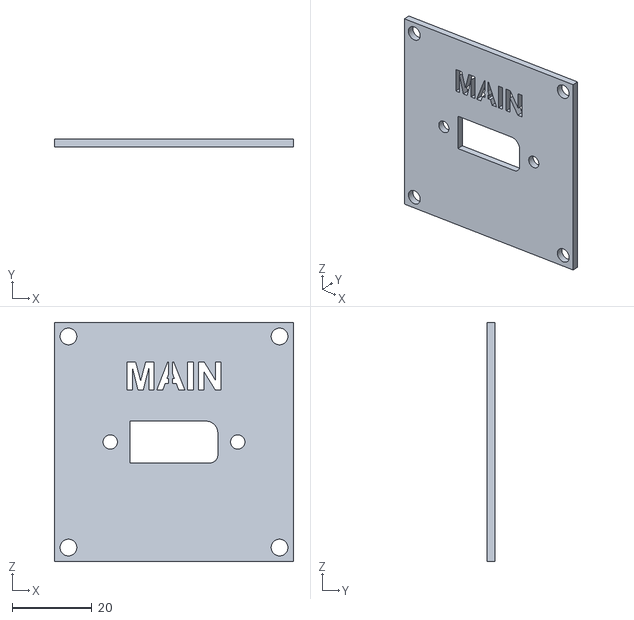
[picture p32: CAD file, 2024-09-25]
print-files/Panel-Main-XT90_d1x1.stl
60.0 x 2.00 x 60.0

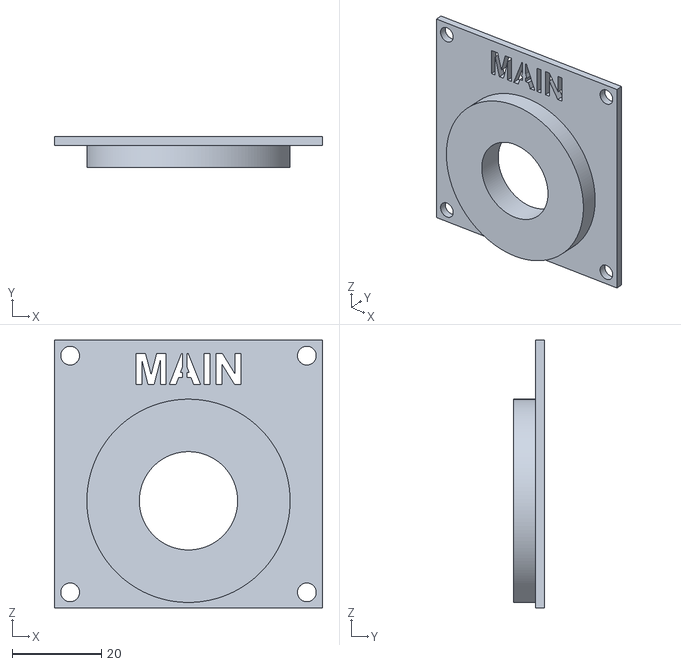
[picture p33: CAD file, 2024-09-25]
print-files/Panel-Main-50A-Switch_d1x1.stl
60.0 x 7.00 x 60.0

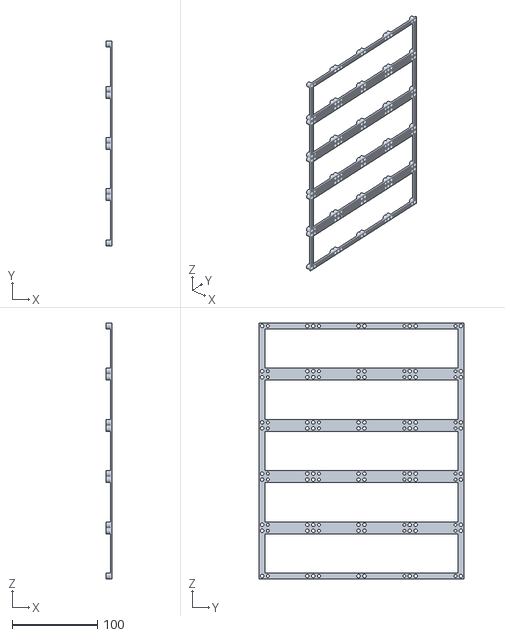
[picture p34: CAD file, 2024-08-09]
print-files/Frame-Complete_x2.stl
7.00 x 240.0 x 300.0

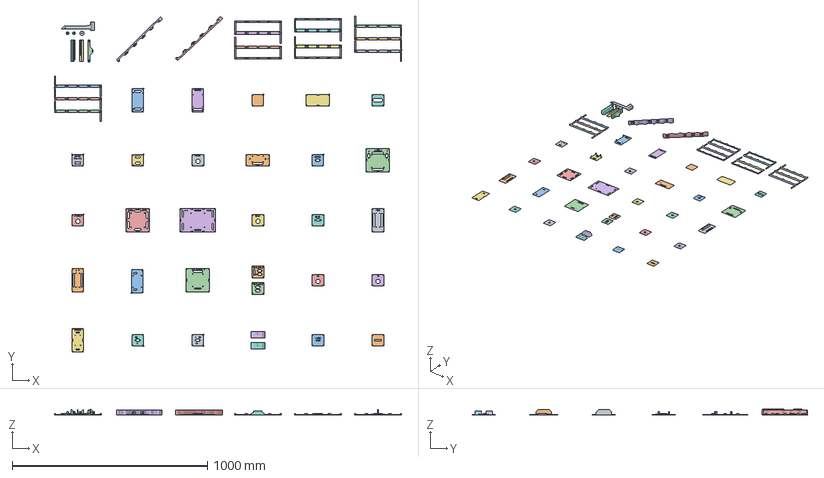
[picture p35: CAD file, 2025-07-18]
bambulab-x1c-print-profile.3mf
1776.5 x 1718.9 x 30.3 mm
Body-Frame-Adapter-top.stl
Panel-Speaker-XT60_d1x1.stl
Panel-AstroCan-AutoDome_d1x1.stl
Panel-Speaker-XT60-V2_d1x1.stl
Panel-Fusebox_d2x2.stl
Stand_x2.stl x 2
Panel-Buck-Converter-12v-20A_d1x1.stl
Panel-Dome-50A-Switch_d1x1.stl
Panel-Blank_d1x1.stl
Panel-AstroCan-Pro-Dual-Shield_d1x2.stl
Frame-Modular-Middle_x6.stl x 6
Frame-Connector-right.stl
Frame-Connector-left.stl
Body-Adapter-left.stl
Body-Adapter-right.stl
Body-Frame-Adapter-top-Knob.stl
Frame-Adapter-pin-left.stl
Frame-Adapter-pin-right.stl
Frame-Connector-top.stl
Frame-Modular-End_x4.stl x 4
Panel-Audio_d1x2.stl
Panel-Blank_d2x1.stl
Panel-Blank-open_d1x1.stl
Panel-Body-Master-MPX_d1x1.stl
Panel-Dome-Slip-Ring-Adapter_d2x1.stl
Panel-Dome-XT60_d1x1.stl
Panel-Double-30A-Relay-Board-Drives-XT60-Connectors_d2x2.stl
Panel-Drives-50A-Switch_d1x1.stl
Panel-Fusebox_d3x2.stl
Panel-Main-50A-Switch_d1x1.stl
Panel-Main-XT90_d1x1.stl
Panel-PDB-12V_d1x2.stl
Panel-PDB-24V_d1x2.stl
Panel-PDB-Modular_d2x1.stl
Panel-Sabertooth-32A_d2x2.stl
Panel-Switch-Left-Leg_d1x1.stl
Panel-Switch-Right-Leg_d1x1.stl
Panel-Syren-10A_d2x1.stl
Panel-XT60-Left-Leg_d1x1.stl
Panel-XT60-Right-Leg_d1x1.stl
Panel-Blank-open-small_d1x1.stl

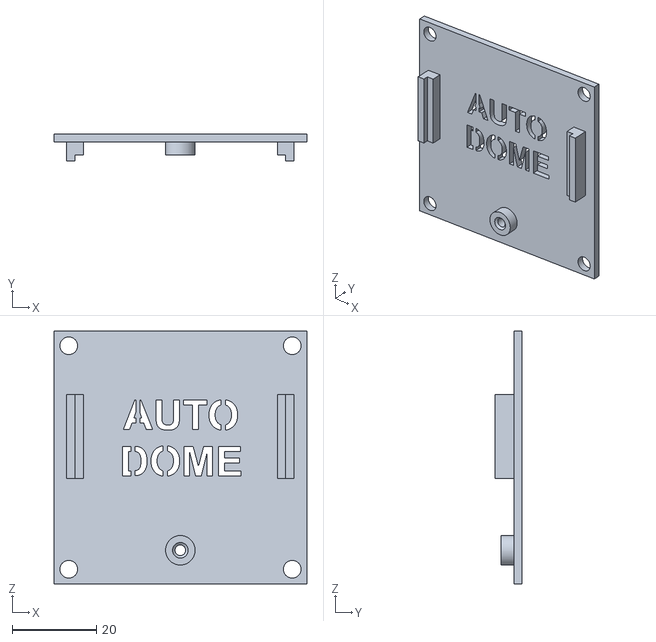
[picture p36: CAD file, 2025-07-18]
print-files/Panel-AstroCan-AutoDome_d1x1.stl
60.0 x 6.50 x 60.0

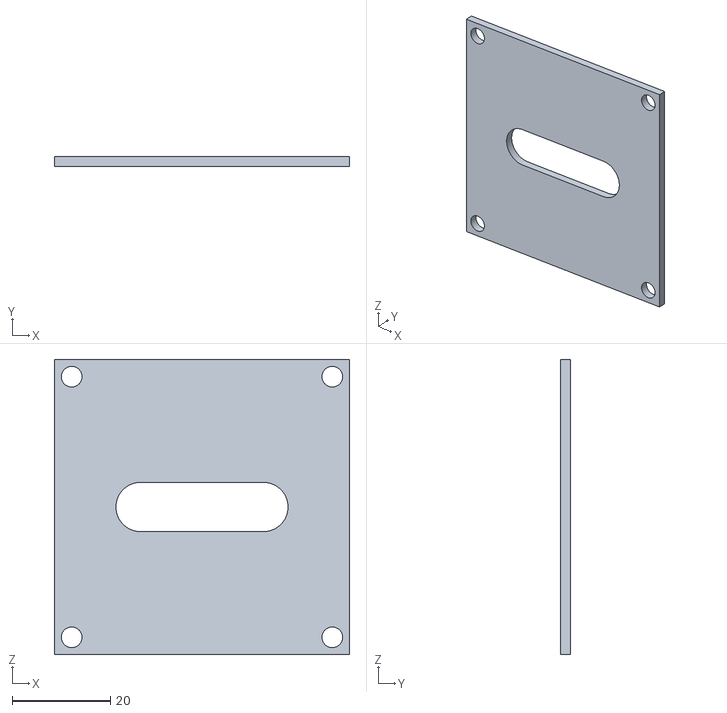
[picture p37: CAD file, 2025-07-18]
print-files/Panel-Blank-open-small_d1x1.stl
60.0 x 2.00 x 60.0

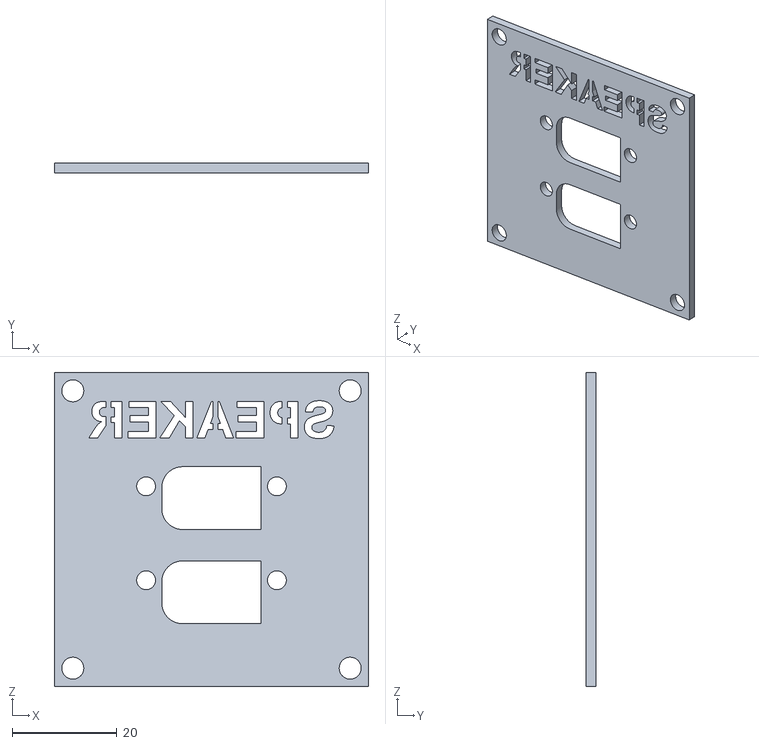
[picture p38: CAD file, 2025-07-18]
print-files/Panel-Speaker-XT60-V2_d1x1.stl
60.0 x 2.00 x 60.0

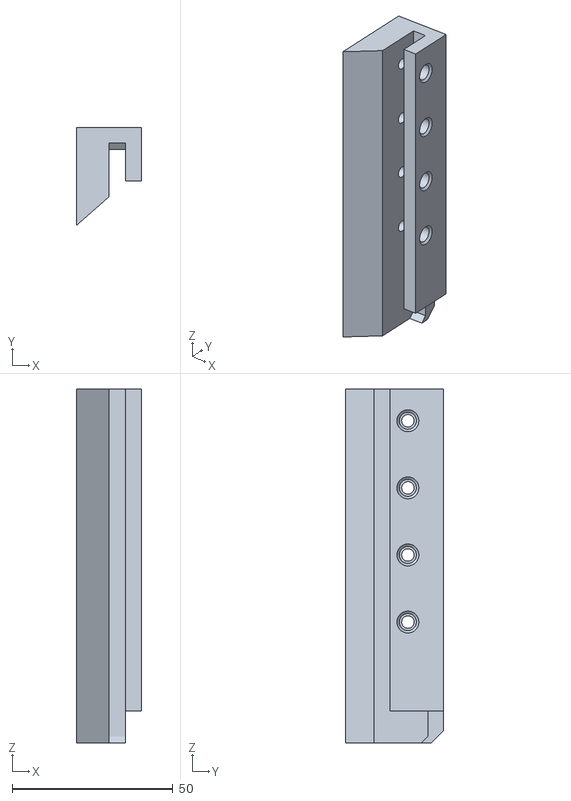
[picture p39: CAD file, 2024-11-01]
print-files/Body-Adapter-right.stl
20.1 x 30.3 x 110.0

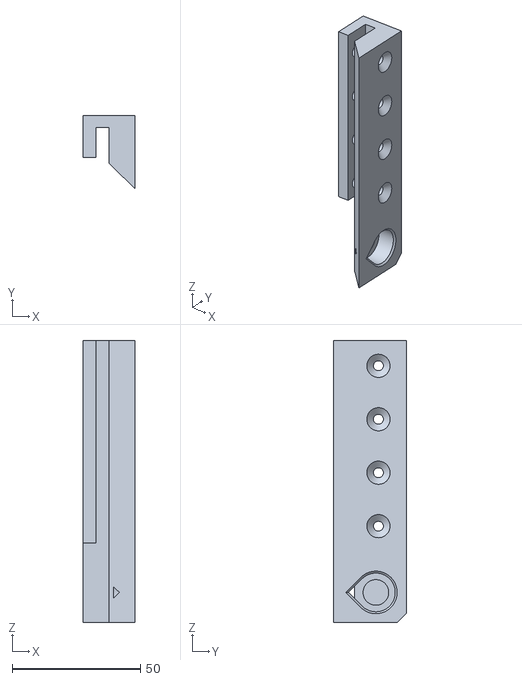
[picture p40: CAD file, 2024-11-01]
print-files/Body-Adapter-left.stl
20.1 x 28.6 x 110.0

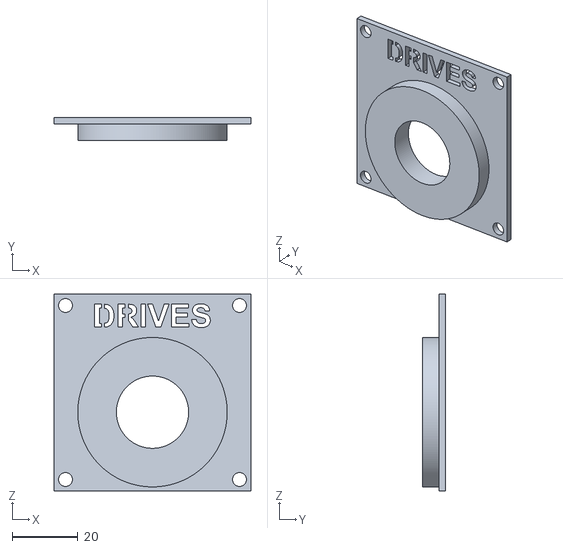
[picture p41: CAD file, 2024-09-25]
print-files/Panel-Drives-50A-Switch_d1x1.stl
60.0 x 7.00 x 60.0

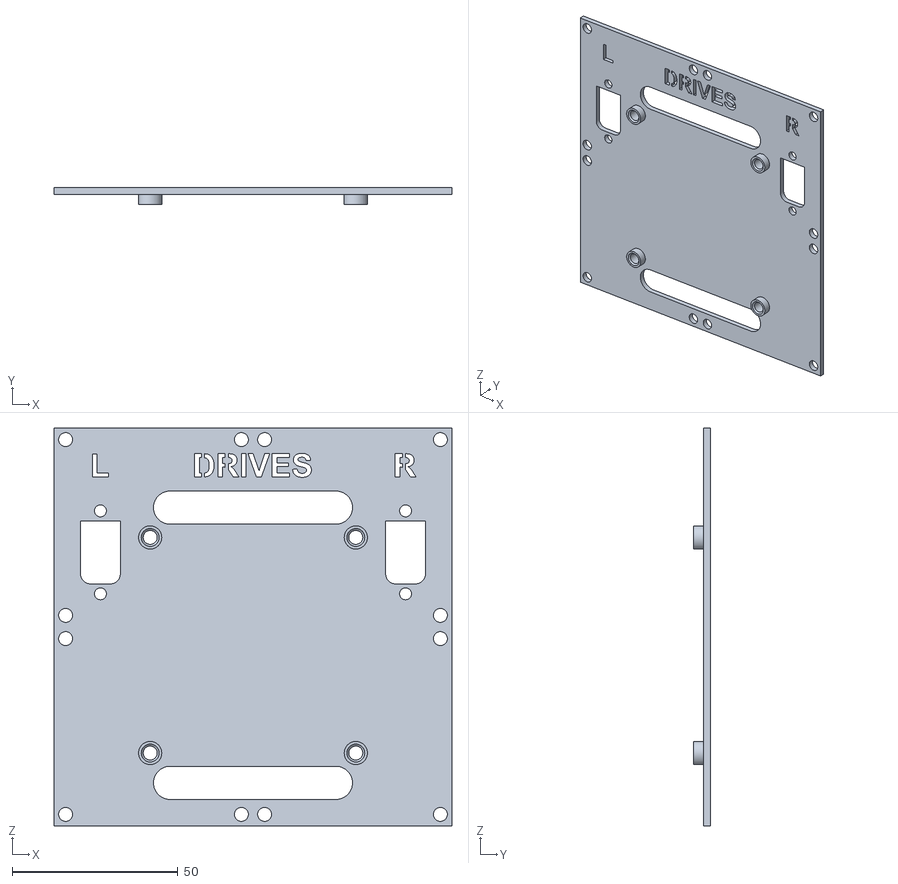
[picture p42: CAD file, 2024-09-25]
print-files/Panel-Double-30A-Relay-Board-Drives-XT60-Connectors_d2x2.stl
120.0 x 5.00 x 120.0

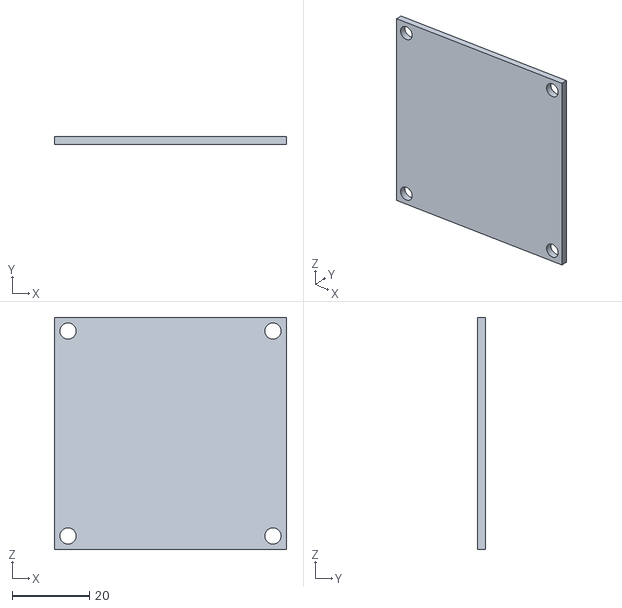
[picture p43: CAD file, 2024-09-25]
print-files/Panel-Blank_d1x1.stl
60.0 x 2.00 x 60.0

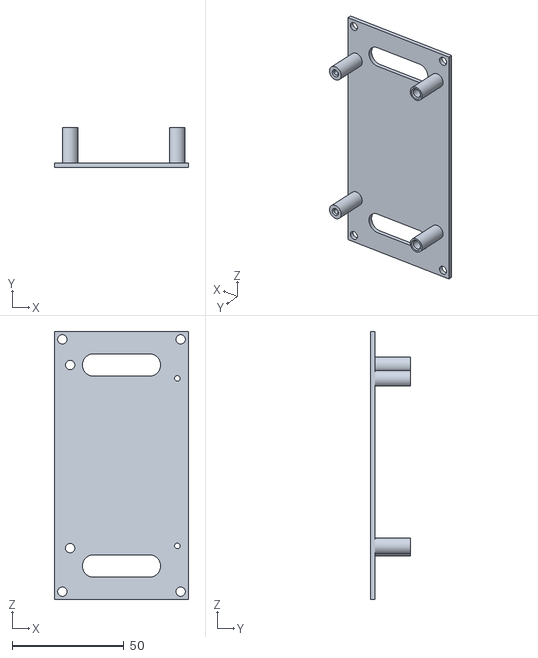
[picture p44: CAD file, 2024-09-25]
print-files/Panel-AstroCan-Pro-Dual-Shield_d1x2.stl
60.0 x 18.0 x 120.0

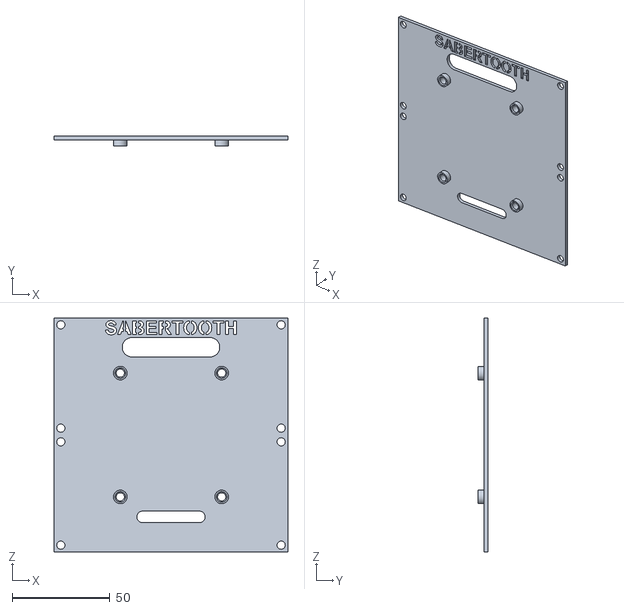
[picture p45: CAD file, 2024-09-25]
print-files/Panel-Sabertooth-32A_d2x2.stl
120.0 x 5.00 x 120.0

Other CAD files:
print-files/Panel-Dome-50A-Switch_d1x1.stl
print-files/Body-Frame-Adapter-top.stl
print-files/Panel-Blank-open_d1x1.stl
print-files/Panel-Audio_d1x2.stl
print-files/Body-Frame-Adapter-top-Knob.stl
print-files/Frame-Adapter-pin-left.stl
print-files/Frame-Adapter-pin-right.stl
print-files/Frame-Connector-Left.stl
print-files/Frame-Connector-Right.stl
print-files/Frame-Connector-Top.stl
print-files/Frame-Modular-End_x4.stl
print-files/Frame-Modular-Middle_x6.stl
print-files/Panel-Blank_d2x1.stl
print-files/Panel-Body-Master-MPX_d1x1.stl
print-files/Panel-Buck-Converter-12v-20A_d1x1.stl
print-files/Panel-Dome-Slip-Ring-Adapter_d2x1.stl
print-files/Panel-Dome-XT60_d1x1.stl
print-files/Panel-Fusebox_d2x2.stl
print-files/Panel-Fusebox_d3x2.stl
print-files/Panel-PDB-12V_d1x2.stl
print-files/Panel-PDB-24V_d1x2.stl
print-files/Panel-PDB-Modular_d2x1.stl
print-files/Panel-Speaker-XT60_d1x1.stl
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

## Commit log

2024-08-09 Initial push
    [Body-Adapter-Left-Bottom.stl, Body-Adapter-Left-Top.stl, Body-Adapter-Right-Bottom.stl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]
2024-08-10 Added images of frame assembly and parts
2024-09-25 Added new images, stls and updated documentation
    [Body-Adapter-Left-Bottom.stl, Body-Adapter-Left-Top.stl, Body-Adapter-Right-Bottom.stl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]
2024-09-25 Updated documentation and added print profile
    [bambulab-x1c-print-profile.3mf]
2024-11-01 Fixed missing bevel, update print file
    [Body-Adapter-left.stl, Body-Adapter-right.stl, bambulab-x1c-print-profile.3mf]
2025-03-24 Fixed wrong mentioned screws for attaching the body adapters to R2
2025-07-18 Added three new panels, updated the documentation
    [Panel-AstroCan-AutoDome_d1x1.stl, Panel-Blank-open-small_d1x1.stl, Panel-Speaker-XT60-V2_d1x1.stl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]
